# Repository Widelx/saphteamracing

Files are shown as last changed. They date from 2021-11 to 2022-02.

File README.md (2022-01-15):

# SaphTeamRacing
Course de voiture autonomes à laquelle participe l'IUT de cachan.
Année scolaire 2021/22.

Programmes MBED, Keil et Octave developpés par Guillaume de Maricourt.
Programmes d'interprétation développés par Antoine Beauvarlet.
PCB carte puissance et carte traitement développés par Axel Manadi.

Ces programmes et PCB sont réservés aux étudiants de l'IUT de Cachan uniquement.

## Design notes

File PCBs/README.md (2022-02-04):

# PCB - Carte DSICOF746NG

Ce dossier contient deux projets de PCBs
- Une première carte d'adaptation entre les différents modules et le microcontroleur F303K8.
- Une seconde carte (obsolète) d'adaptation entre les différents modules et la carte de contrôle DISCO F746-NG.

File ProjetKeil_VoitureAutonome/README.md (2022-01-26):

# Projet KEIL

Ce dossier contient une ébauche très succinte d'un projet keil qui initialise différents composants (PWM, UART).
Ce programme n'est absolument pas complet et n'est pas utile dans la version atuelle après migration sur la cible DISCO F746NG.
Cependant celui-ci à terme devrait être utile pour la carte KEIL développée.

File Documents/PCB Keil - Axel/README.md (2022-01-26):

Ceci contient le PCB ainsi que les shematics d'une carte Keil adaptée aux dimensions de la maquette de la voiture.

Logiciel : ALTIUM designer 2004

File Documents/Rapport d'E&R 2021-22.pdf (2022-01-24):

## Rapport d’Etude et Réalisation

## Année Universitaire 2021-2022, Semestre 3

# SAPH TEAM RACING

## Course de voitures autonomes

Présenté par : Antoine Beauvarlet,

## Axel Manadi, Guillaume Dumesnil

Janvier 2022

## Sous la direction de M. Martincic et M. Bellanger

Guillaume Dumesnil, Antoine Beauvarlet, Axel Manadi
Rapport E&R, S3
Janvier 2022 | 2

# Remerciements

Nous tenons à remercier toutes les personnes qui ont contribué au succès de notre projet et

qui nous ont aidés lors de la rédaction de ce rapport.

Nous voudrions dans un premier temps remercier M. Martincic, professeur d’Etude et

Réalisation à l’IUT de Cachan, pour sa patience, sa disponibilité et surtout ses judicieux

conseils, qui ont contribué à la réussite de ce projet.

Nous remercions notre professeur de Culture et Communication M. Bellanger qui nous a

guidé dans la rédaction du rapport.

Également, nous tenons à remercier M. Ardillier ainsi que tout le corps enseignant de l’IUT

de Cachan pour avoir assuré le bon déroulement de nos différentes séances et permis, à

terme, de mener à bien ce projet semestriel.

Enfin, merci à nos camarades de promotion avec lesquels nous avons échangé sur nos

projets respectifs.

# Résumé

Notre projet de troisième semestre consiste à créer une voiture électrique autonome

capable de se déplacer sans intervention humaine.

Pour ce projet, nous avions besoin de plusieurs cartes électroniques que nous avons

élaborées avec pour objectif de tenir dans le châssis du véhicule. Un moteur brushless

relié aux quatre roues motrices ainsi qu’un servomoteur assurent le déplacement de la

voiture. Tous les composants ont été assemblés sur un châssis de Lancia Delta de

modélisme.

Pour rendre le véhicule autonome, nous l’avons équipé de capteurs infrarouges et à

ultrasons ainsi que d’un LiDAR. Par ailleurs un module Bluetooth est connecté au

microcontrôleur afin d’assurer une transmission sans fil et de collecter les données perçues

en temps réel.

Pour la conception et la réalisation de ce projet, nous avons eu besoin de passer par

plusieurs logiciels : Altium pour la conception des cartes électroniques, Mbed Studio et

MBed.org pour la programmation des microcontrôleurs DISCO F746-NG ainsi que le logiciel

Octave pour la visualisation des données en temps réel.

# Sommaire

# Introduction

À l'IUT de Cachan dans le département GEII2 les étudiants de S3 réalisent un projet

semestriel qu'ils choisissent. Ce projet semestriel a pour objectif de mettre en application les

connaissances acquises en génie électrique (TEC*

1
, SA*, CE*), physique, mathématiques et

programmation (IENA*).

Notre groupe, constitué de trois élèves, s’est donné comme objectif de créer une voiture

autonome pour participer à une course organisée en avril 2022 où concourent diverses

écoles d’ingénieurs et universités. Dans ce contexte notre problématique est d’obtenir un

véhicule capable d’interagir avec son environnement sans opérateur humain, et sans

collision avec les autres véhicules ou obstacles.

Ce projet de voiture autonome nous a permis de travailler en petit groupe avec des sous-

tâches attribuées à chacun des membres. Cela permet d’appréhender concrètement

l’électronique, la programmation, la mécanique et surtout le travail en équipe.

Travailler en groupe permet de se répartir les tâches selon nos spécialités, afin de respecter

les délais et d’être plus efficace. De plus nous sommes obligés de rendre compte au groupe

et respecter nos engagements.

Bien entendu durant tout ce projet notre professeur peut être sollicité, afin de nous

accompagner et de nous faire progresser. Au début du semestre, chaque groupe d’étudiant

du semestre 3 a préparé une soutenance afin de présenter les objectifs de leur projet et ont

livré un diagramme de Gantt* prévisionnel.

Contrairement aux semestres précédents, ce projet nous plonge dans une situation presque

professionnelle : définir et répondre à un cahier des charges tout en prévoyant et respectant

les délais de livraison.

Dans un premier temps, nous présenterons la mécanique de la voiture, puis nous étudierons

les différentes cartes électroniques réalisées. Ensuite, nous examinerons comment la

réception des données constituant l’environnement est réalisée puis comment l’interprétation

de celles-ci s’effectue. Enfin nous conclurons.

1 Les mots accompagnés d’une * sont des mots définis dans le lexique à la fin de ce document.

# Présentation du projet

Lors du semestre 3 nous avons pu choisir notre projet : une course de voitures autonomes.

Ce projet, organisé depuis longtemps, consiste à récupérer le travail que le groupe de

l’année dernière a produit et le continuer. Ainsi notre groupe a pu, en s’appuyant sur le

rapport du groupe précédent, améliorer, repenser les concepts de programmation et

recommencer certaines parties.

Nous sommes partis d’un châssis de Lancia Delta de modélisme, imposé par le règlement

de la course, que nous avons adapté pour recevoir nos capteurs. Le travail du groupe

précédent ayant concerné l’assemblage du véhicule, cela nous a permis de nous focaliser

sur l’instrumentation de celui-ci.

Nous avons dû concevoir des cartes imprimées : carte de puissance et carte d’acquisition.

Puis mettre en œuvre des capteurs afin de modéliser l’environnement et générer une

réflexion sur les comportements de la voiture.

Ces 3 grandes tâches réparties sur le groupe ont été effectuées plus ou moins de façon

asynchrone. Les deux cartes imprimées sur lesquelles nous reviendrons plus tard, répondent

aux besoins suivants :

- Carte d’acquisition : contrôler les capteurs et modéliser l’environnement.
- Carte de puissance : générer une réponse au modèle et piloter les moteurs.

Toutes ces étapes sont détaillées dans la suite de ce rapport et en annexes²

## - Les règles de la course

## 1. Le cahier des charges

Lors de la course nous serons mis en compétition contre 5 autres véhicules autonomes. La

course s’effectue en 3 tours.

2 Afin de rendre synthétique ce document nous avons préféré placer certaines informations en annexe. De plus un repository GitHub a été mis en place pour transmettre la totalité de notre travail.

Pour y participer, nous devons nous plier au cahier des charges rédigé par les

organisateurs :

- Véhicule issu d’un kit de modélisme de Tamiya TT-02.
- Découpe de la carrosserie à condition qu’elle recouvre 80% du véhicule.
- Batterie de type NiMH* de 7,2V.
- Dimensions imposées afin d’être détectable (voir la figure suivante).
- Peinture n’absorbant pas les longueurs d’onde infrarouges.
- Contact bluetooth au moins 1 fois par seconde avec un appareil immobile (arrêt du

véhicule sinon).

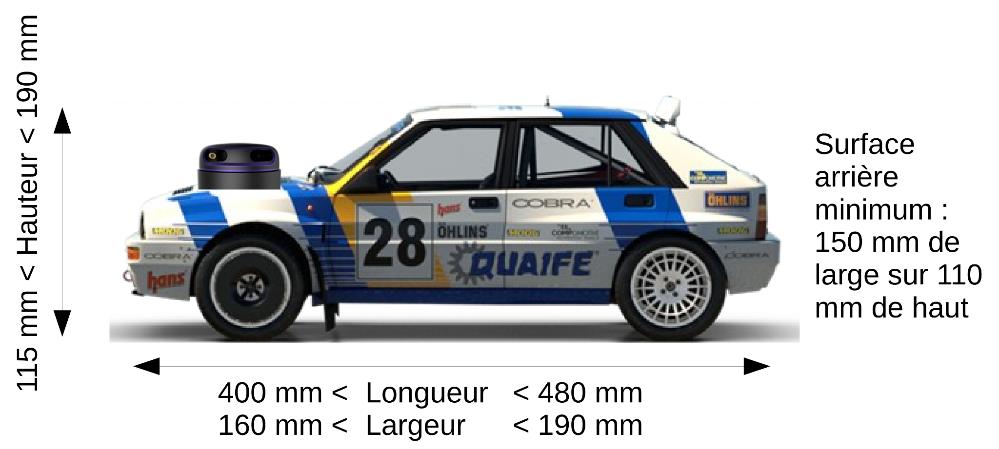
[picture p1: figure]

FIGURE 1: DIMENSIONS REGLEMENTAIRES DU VEHICULE

Concernant les capteurs, nous sommes libres dans le choix des capteurs tant qu’un capteur

LiDAR* est l'élément principal de détection de notre véhicule.

Pour s’assurer que les véhicule répondent au cahier des charges, les organisateurs

procéderont, lors de la course, à une homologation de ceux-ci.

## 2. Le circuit

Nous découvrirons le tracé du circuit le jour de la course. Actuellement nous sommes

uniquement informés des mesures de la piste. Celle-ci aura des bordures de 20 cm de

hauteur avec une largeur minimum en tout point de 50 cm. Par ailleurs elle contiendra des

obstacles conformément à l’exemple donné ci-dessous.

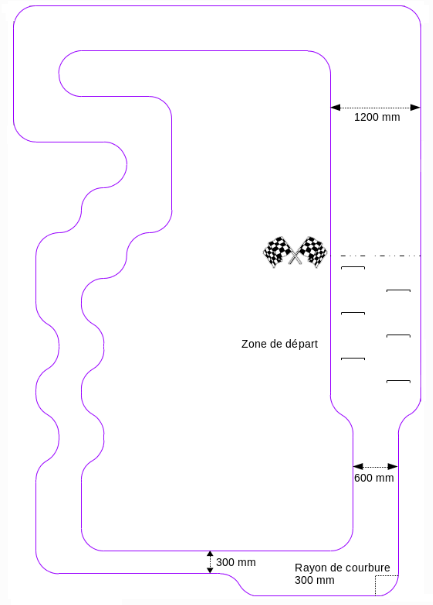
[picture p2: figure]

FIGURE 2: EXEMPLE DE PARCOURS FOURNI PAR LES ORGANISATEURS

Pour remporter cette compétition, il faut passer des qualifications sur une première piste,

chaque véhicule la parcourant seul. Deux passages sont exigés : un premier sans obstacle

puis un second avec. Chacune des qualifications nécessite deux passages successifs

réussis, c’est-à-dire sans collision avec les obstacles.

La somme des temps des deux passages détermine ensuite l’ordre de passage. Chaque

équipe dispose uniquement de 3 minutes pour préparer le véhicule sur la piste. Après ce

délai, aucune intervention humaine n’est tolérée.

## - Schéma synoptique du véhicule

Nous avons réalisé un schéma synoptique* afin de synthétiser et d’appréhender

l’assemblage des composants électriques qui constituent la voiture.

FIGURE 3: SCHEMA SYNOPTIQUE DU PROJET

FIGURE 4: LEGENDE DU SCHEMA SYNOPTIQUE

## - Diagramme de Gantt prévisionnel

Pour la soutenance de début de projet et répondre de manière professionnelle au cahier des

charges, nous avons réalisé un diagramme de Gantt prévisionnel. Celui-ci, bien qu’optimiste,

nous a permis de saisir une chose importante. En effet il faut prendre en compte qu’un projet

est souvent constitué de difficultés imprévisibles tant en quantité qu’en temps nécessaire

pour les résoudre. Le diagramme prévisionnel ci-dessous n’a effectivement pas pu être

respecté en totalité.

Cependant nous avons effectué plus de 80 % du prévisionnel, ce que l’on peut constater sur

le « diagramme de Gantt effectif » ci-dessous, qui reprend le calendrier que nous avons

effectivement suivi. Nous pouvons considérer notre estimation comme une réussite.

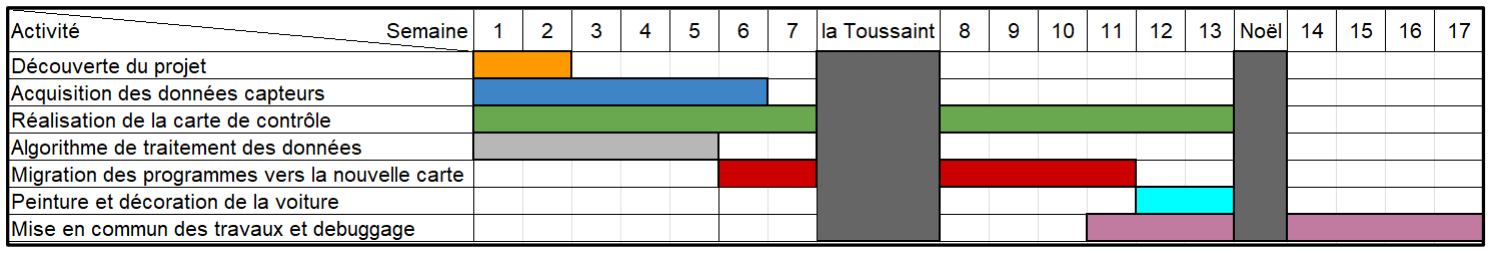
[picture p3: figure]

FIGURE 5: DIAGRAMME DE GANTT PREVISIONNEL

FIGURE 6: DIAGRAMME DE GANTT EFFECTIF

# Conception des PCB

## - Carte de puissance

Pour que le véhicule puisse se diriger durant la compétition, il faut créer une carte qui puisse

communiquer des instructions aux actionneurs présents sur le véhicule :

- Un servomoteur, pour la direction
- Un moteur brushless, pour avancer ou reculer.

La carte de puissance va communiquer avec les actionneurs grâce à un signal nommé PWM

(Pulse Width Modulation ou Modulation de Largeur d'Impulsion), qui est un signal alternatif

TOR (tout ou rien).

Ce signal alternatif, avec des vitesses de commutation très rapides, permet de d’approximer

la tension sur la liaison grâce notamment à l’inertie des moteurs : la tension ne devient plus

une série de commutations « 0/1 » mais une tension moyenne ajustable par un rapport

cyclique α.

FIGURE 7: EXEMPLE DE SIGNAL PWM.

Par ailleurs cette carte devra obéir aux instructions d’une unité de traitement comme une

autre carte par exemple. Il faut donc ajouter un moyen de communication.

## - Carte de communication

En plus de conduire le véhicule, nous avons besoin de traiter les données fournies par les

différents capteurs embarqués.

La carte communication recevra donc des informations de la part de :

- 1 capteur LiDAR (capteur principal).
- 3 capteurs à ultrasons (capteurs auxiliaires).
- 3 capteurs infrarouges (capteurs auxiliaires).

Dans cette carte nous allons téléverser un programme qui s’occupe de l'acquisition des

données, c'est-à-dire décoder ce que chaque capteur transmet. Celle-ci comprendra

également un algorithme décisionnel afin d’orienter le véhicule en fonction de

l'environnement : prendre un virage, éviter un obstacle ou une autre voiture par exemple.

On en déduit donc un rôle de carte maître vis-à-vis de la carte de puissance, car elle lui

donnera les instructions à exécuter. Enfin cette carte générera le signal PWM de commande

du lidar.

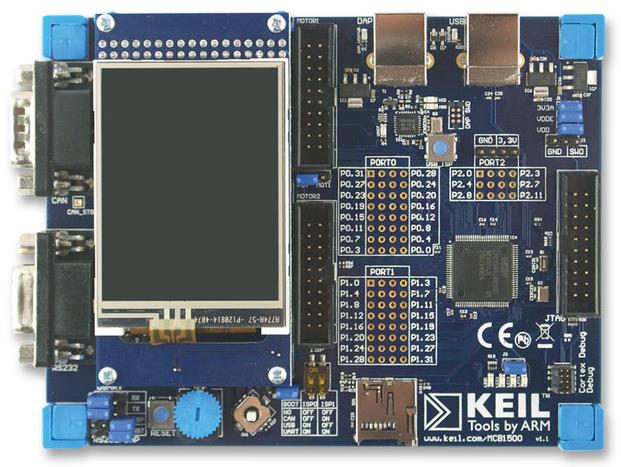
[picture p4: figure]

FIGURE 8: CARTE KEIL UTILISEE EN TP DE IENA

Nous avons commencé à réaliser cette carte, sur le modèle de la « carte Keil » de TP.

Malheureusement nous n’utiliserons pas cette dernière car elle ne sera achevée dans les

temps.

## - Conception des cartes

Pour concevoir ces deux cartes, nous avons utilisé le logiciel de CAO* : « Altium Designer ».

Plus précisément la version « 20.2.4 » du logiciel.

FIGURE 9: LOGO DU LOGICIEL ALTIUM DESIGNER

Une licence ainsi que des manuels d’utilisation nous ont été fournis, pour faciliter la prise en

main de cet outil professionnel.

Afin de trouver les composants nécessaires à la création de notre carte nous avons eu accès

aux bibliothèques de composants de l’université et des projets des années précédentes.

L’utilisation de ce logiciel est enrichissante : elle permet de découvrir le fonctionnement d’un

outil professionnel largement utilisé dans le monde de l’industrie.

Nous allons détailler, ci-dessous, les étapes à suivre pour réaliser un PCB.

## 1. Création d’un schéma

En premier lieu il faut créer un schéma : le but de cette opération est de placer les

composants et de les relier par des liaisons électriques théoriques. Cela permet de savoir

quels composants communiquent électriquement entre eux.

Notre professeur d’étude et réalisation, M. Martincic, nous a fourni le schéma des « cartes

Keil » utilisées à l'université durant les TPs d’IENA. Après une étude du schéma nous

remarquons que cette carte possède de nombreux composants superflus pour l’utilisation

que nous souhaiterions en faire.

Notre première mission consistait donc à supprimer les composants inutiles (et leurs

connexions) afin de simplifier le schéma et d’optimiser les performances de notre

microcontrôleur.

Une fois cette étape passée nous avons dû intégrer de nouveaux composants.

Un fichier contenant les fonctions de chaque broche de notre contrôleur nous a été fourni,

afin de relier chacun des composants à sa fonction associée.

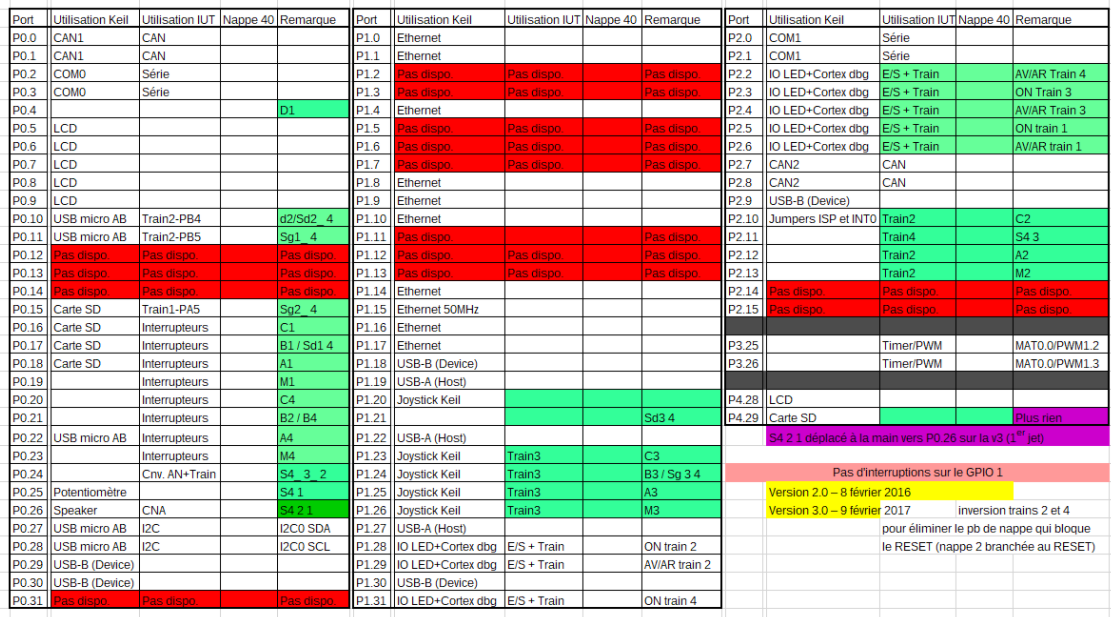
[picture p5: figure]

FIGURE 10: TABLEAU EXCEL DES FONCTIONS DU MICROCONTROLEUR

Nous avons laissé des ports CAN* pour que la carte puisse communiquer et recevoir des

informations ou instructions de la part d’un ordinateur (ou un autre microcontrôleur).

Après avoir relié chaque composant, nous pouvons passer à la deuxième étape : le câblage

du PCB*.

## 2. Câblage du PCB

Nous avons donc une nouvelle interface qui est une modélisation de la carte (réelle)

que nous allons imprimer. Pour que notre carte fonctionne correctement nous devons

effectuer le routage de celle-ci.

Cette étape, indispensable, consiste à tracer les pistes qui permettent de transmettre

l’information et d’alimenter les composants du circuit. Dans notre cas nous avons réussi à

nous limiter à une carte avec des pistes sur les deux couches externes (ce qui réduit

considérablement les coûts de production).

Positionner les composants sur les deux côtés de la carte permet une meilleure organisation

pour le routage. Le routage des cartes respecte une règle implicite et universelle : les pistes

ne doivent pas se croiser sur une même couche et ne doivent pas former d’angles droit.

Pour éviter que les pistes se rencontrent, on utilise des « via(s) » qui sont des outils qui

permettent de passer une connexion électrique d’une couche à l’autre.

Enfin quand le PCB est réalisé, nous devons faire un plan de masse. Cela consiste à

connecter chaque composant à une masse, pour que ceux-ci aient une tension de référence

commune et puissent fonctionner en régime nominal.

Remarque : Idéalement dans un véhicule il est recommandé de relier la masse au châssis

du véhicule. Dans notre cas le châssis est en plastique et cela ne fonctionnerait pas. Relier

la masse au châssis permet d’augmenter la surface de la tension de référence et d’être

moins sujet à des perturbations, par exemple les perturbations électromagnétiques que

génère le moteur.

Quand le plan de masse est finalisé, nous pouvons passer à la dernière étape : imprimer la

carte et souder les composants sur la carte.

## 3. Soudure des composants

Avant de procéder à la soudure, nous devons effectuer une commande qui va regrouper les

éléments de notre PCB. Cette commande demande d’inclure un fichier Gerber (format

standard, norme « d’impression ») qui pourra être reconnu et utilisé par les machines de

découpe des circuits.

Pour souder les composants nous utilisons la méthode de soudure à l’étain chaud : nous

fixons les différents composants du circuit à l’emplacement qui leur est dédié et nous venons

appliquer de l’étain sur les pattes des composants. Cela permet la connexion électrique

entre la piste et le composant.

Pour s’assurer du bon fonctionnement de la carte, nous effectuons des tests de connexion

des pistes. De plus nous devrons mettre en place des protocoles, simples, pour vérifier le

bon fonctionnement de chacun des composants assemblés.

FIGURE 11: IMAGE DE MICROSOUDURE

## - Problèmes rencontrés

Le problème principal des PCB est que les éléments constituants ces derniers fonctionnent

soit en 5, soit en 3,3 volts. Or notre alimentation fournit une tension de 7,2 volts, tension trop

importante qui pourrait abimer les composants.

Pour résoudre ce problème nous pensions tout d’abord ajouter un régulateur de tension qui

aurait eu pour rôle d’abaisser la tension d’alimentation. Cependant nous en avons discuté

avec notre professeur qui nous a déconseillé de le faire. Cela induirait des courants

importants qui provoquerait des perturbations sur les composants de notre carte.

Nous suivons donc le conseil de notre enseignant, et nous allons ajouter une carte

supplémentaire qu’il a réalisé pour pallier ce problème.

FIGURE 12: BATTERIE UTILISEE DANS NOTRE PROJET

Après avoir été capable de relier entre eux les composants nous devons les piloter. Ce

pilotage passe par la compréhension des composants que nous allons traiter. La partie

suivante traitera donc ce sujet.

# Modélisation de l’environnement

La voiture, pour interpréter et interagir avec son environnement, doit savoir comment celui-ci

est constitué. Pour ce faire le véhicule fait appel à divers capteurs qui permettent de

cartographier l’espace dans lequel il se déplace.

Cependant utiliser des capteurs implique divers délais qui compliquent la tâche :

- Un premier délai imposé par le principe de fonctionnement physique du capteur.
- Un second délai imposé par le type de transmission des informations.

Ainsi pour rendre efficace la tâche de reconnaissance de l’environnement, nous utiliserons 3

capteurs différents avec des positionnements sur le châssis bien spécifiques : 3 capteurs à

ultrasons et 3 capteurs infrarouges que nous appellerons des capteurs de proximité et un

LiDAR.

## - Le LiDAR

## 1. Principe de fonctionnement d’un LiDAR

Le capteur LiDAR pour « Light Detection And Ranging » est un système opto-électronique*

qui permet de mesurer des distances. Le fonctionnement repose sur un capteur infrarouge

monté sur un moteur : en actionnant le moteur, le capteur infrarouge tourne sur lui-même.

Le capteur infrarouge envoie ensuite des impulsions laser régulières qui sont perçues après

avoir été réfléchies sur un obstacle. Ainsi, plus la lumière émise met de temps à revenir, plus

l’obstacle est loin. Cela permet de faire des mesures de distance qui sont associées à un angle et de créer une carte de l’environnement très précise³

3 Le LiDAR utilisé dans notre cas est de la marque SLAMTEC, modèle A2, dont la documentation n’est pas simple à comprendre en début de projet. Nous essaierons d’être le plus précis possible pour simplifier la prise en main du projet.

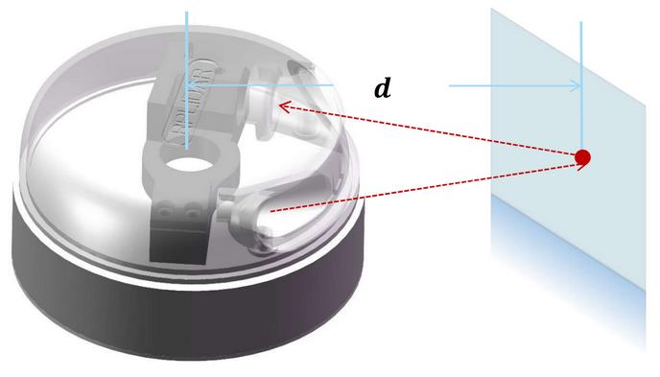
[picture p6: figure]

FIGURE 13: MODELE DE FONCTIONNEMENT DU LIDAR

FIGURE 14: REPRESENTATION PRECISE DU FONCTIONNEMENT DU LIDAR

Le LiDAR, en fonctionnement normal, effectue 2000 mesures par secondes. Le réglage du

signal PWM généré pour contrôler le moteur de celui-ci permet d’ajuster la précision du

LiDAR.

- Si le moteur tourne très vite nous aurons peu de mesures par tour mais beaucoup de

tours par seconde à analyser.

- S’il tourne très lentement nous aurons beaucoup de mesures pour un tour mais peu

de tours par seconde à analyser.

## 2. La transmission des informations

- L’interprétation des trames

La transmission des informations captées par le LiDAR se fait au moyen d’une liaison série

(RS232) dont nous étudierons le fonctionnement plus tard. La bonne compréhension des

données transmise nécessite de s’approprier le concept de trames (ou encodage

d’informations sur plusieurs octets) que nous allons détailler ici.

Une trame informatique est, par définition, « une structure de base d'un ensemble de

données encadrée par des bits de début et des bits de fin ». Cela veut simplement dire

qu’une trame est un assemblage de bits qui sont liés à diverses informations.

Dans notre cas, UNE trame transmise par le LiDAR contient 3 informations utiles associées à une mesure (ou un point⁴
).
- La qualité de la mesure.
- L’angle de la mesure.
- La distance associée à cet angle.

Cette trame est un assemblage de 5 octets avec la répartition de l’information détaillée sur la

figure suivante, selon la documentation du constructeur. De cette lecture on peut retenir la

chose suivante. Sur une trame constituée de 5 ∗ 8 = 40 bits nous avons :

- La qualité sur les bits 2 à 7 (6 bits).
- L’angle sur les bits 9 à 23 (15 bits).
- La distance sur les bits 24 à 39 (16 bits).

4 Par la suite nous supposerons qu’une mesure (une trame) correspond à un point (en coordonnées polaires).

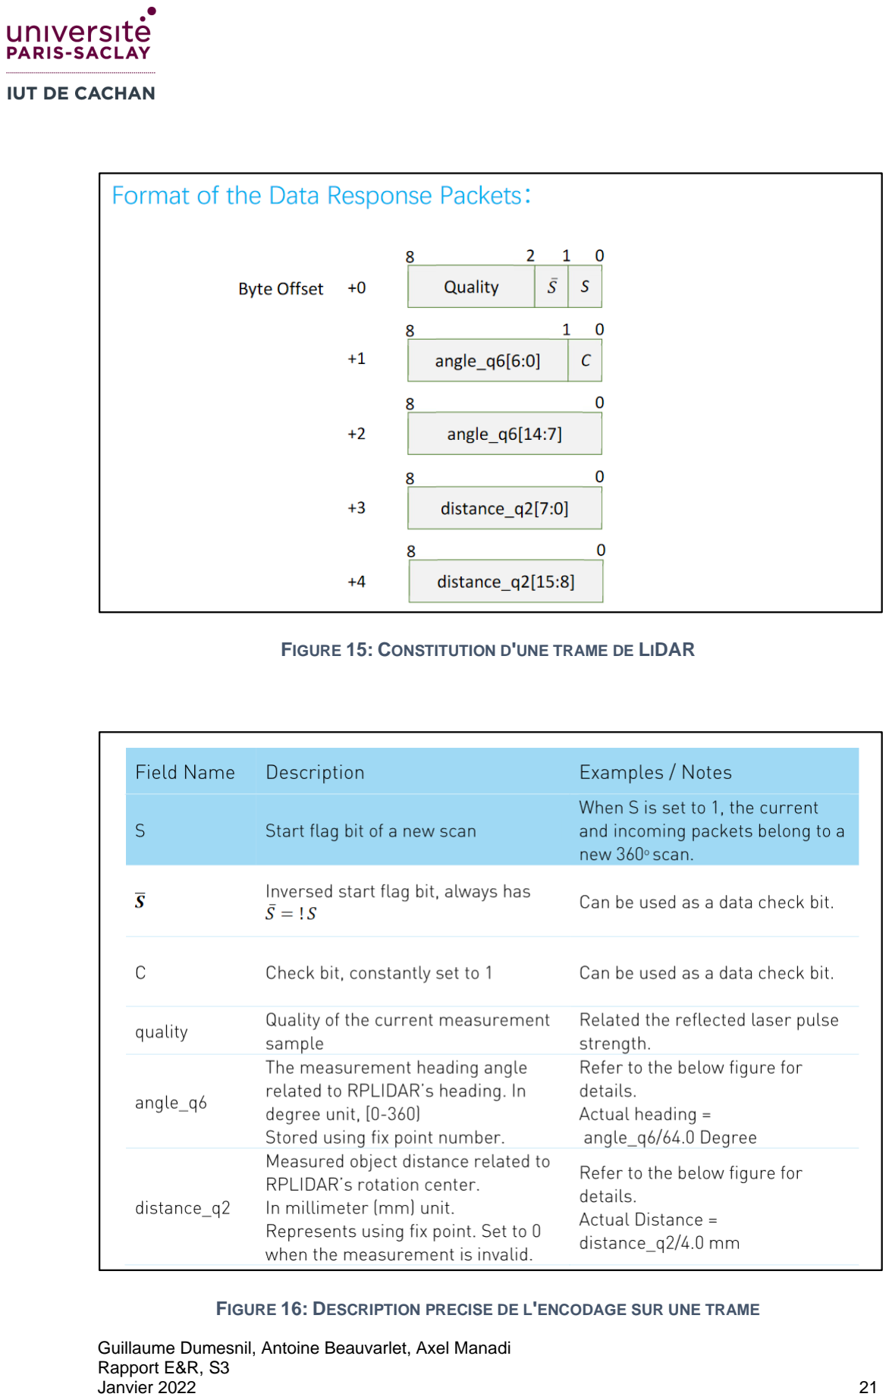
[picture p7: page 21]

FIGURE 15: CONSTITUTION D'UNE TRAME DE LIDAR

FIGURE 16: DESCRIPTION PRECISE DE L'ENCODAGE SUR UNE TRAME

Ainsi en réceptionnant les trames dans un tableau de 5 caractères (un caractère

correspondant à un octet) il est très simple de reconstituer la distance, l’angle et la mesure

d’un point. Voici trois exemples de fonctions qui reconstituent l’information en prenant les

octets correspondants en argument.

Remarque : Il existe cependant deux nuances essentielles pour décoder ces trames. La

valeur binaire de la distance doit être convertie en flottant puis divisée par 4. La valeur sera

alors en millimètres. De même pour l’angle avec une conversion en flottant divisée par 64 pour obtenir des degrés⁵

FIGURE 17: FONCTIONS DE DECODAGE DES TRAMES

On notera la présence d’une saturation numérique sur la valeur de la distance. Dans notre

cas voir à 16 m n’est pas utile et permettra une interprétation plus simple des données.

Nous verrons par la suite que selon le modèle d’exploitation des données, ces trames

contiennent deux autres informations utiles : S et /S ainsi que C. Cela permettra de mettre en place un algorithme de synchronisation ou de vérification de synchronisation⁶

5 Ces informations se trouvent sur la Figure 4.

### 6 Se référer à la sous-partie « Désynchronisation des trames »

Maintenant que nous avons compris de quoi est constituée une trame il nous reste à définir

les instructions à envoyer au LiDAR pour le piloter. Nous verrons la mise en œuvre de la

communication LiDAR<->Microcontrôleur dans la partie suivante.

- Les commandes pour piloter le LiDAR

Le LiDAR, pour fonctionner, doit recevoir des instructions de la part du microcontrôleur. Ces

instructions qui sont proches du concept de trames permettent de changer l’état du LiDAR.

Les instructions ont nous aurons besoin sont présentés ci-dessous avec leur instruction

machine associée.

FIGURE 18: TABLEAU DES INSTRUCTIONS MACHINE

On observe que l’octet n°1 est toujours le même : 0xA5. En effet cet octet quand il est

envoyé averti le LiDAR qu’il va recevoir une instruction dans la milliseconde suivante. Si

aucune information n’est envoyée (octet 2), le LiDAR reste dans son état actuel.

Sous cet aspect, piloter le LiDAR semble très simple. Malgré tout il existe des informations

importantes à savoir pour chacune des instructions.

- Utilité de la fonction Reset

La fonction Reset permet de redémarrer le système du LiDAR. Il peut être nécessaire

de le faire si l’on détecte un défaut de fonctionnement de la part du LiDAR. Par exemple si

l’on ne reçoit pas de réponse de celui-ci.

Conclusion : Faire un reset lors de la mise en route du LiDAR permet de s’affranchir de

certains problèmes.

- Différence entre les fonctions Scan et ForceScan

La fonction Scan nécessite que la vitesse de rotation du LiDAR soit stable avant que

celui-ci n’envoie des points en réponse à l’instruction. La fonction ForceScan permet de

s’affranchir de cette nécessité et permet d’avoir des mesures plus rapidement.

| Trame complète
Instruction | Octet 1 | Octet 2
Stop | 0xA5 | 0x25
Reset | 0xA5 | 0x40
Scan | 0xA5 | 0x20
ForceScan | 0xA5 | 0x21

Ainsi il semble préférable de toujours utiliser ForceScan et non Scan lors du déploiement du

logiciel pilote. Cependant la fonction ForceScan ne permet pas d’assurer la continuité des points⁷
, c’est-à-dire la stricte croissance de l’angle.

Conclusion : Il est préférable d’utiliser la fonction Scan lors du déploiement de la version

finale du software et ForceScan uniquement pour débugger.

Lorsqu’on lui envoie une demande de scan le LiDAR répond par une trame type. Celle-ci est

constituée de sept octets : deux octets de synchronisation et cinq octets (une trame

complète) pour indiquer l’instruction interprétée par le LiDAR.

Après cela le LiDAR envoie en continu des trames sans s’arrêter, sauf si on le lui demande.

Remarque : Il est important de comprendre qu’une trame équivaut à un paquet de 5 octets.

Ainsi un problème de synchronisation ou une perte de trame (non envoyée, mal

réceptionnée) entraine des interprétations erronées qui rendent l’utilisation du LiDAR impossible⁸

FIGURE 19: REPONSE DU LIDAR A UNE REQUETE "SCAN"

Maintenant que nous avons compris du point de vue théorique comment piloter le LiDAR et

interpréter ses données nous allons voir comment cela est réalisé en utilisant un

microcontrôleur.

## - Acquisition des données LiDAR

Afin de réaliser l’acquisition des points collectés par le LiDAR de façon efficace il est

nécessaire de définir plusieurs aspects de cette acquisition.

1) Le fonctionnement physique de la communication « microcontrôleur<->LiDAR ».
2) Les outils informatiques mis à disposition en C/C++.
3) Les couches de communication et les objectifs de notre programme.

7 Se référer à l’annexe « 1 : Continuité des points » pour plus d’informations à ce sujet.

### 8 Se référer à la sous-partie « Désynchronisation des trames »

De ces 3 points nous pouvons constituer des algorithmes, plus ou moins efficaces, qui

acquièrent les trames envoyées par le LiDAR. L’algorithmie de l’acquisition des points

constitue une partie en elle-même. Celle-ci reposant sur des bases nous allons voir, nous y

reviendrons donc plus tard.

## 1. Le protocole de communication : la liaison RS232

La liaison série RS232 asynchrone

9 est un type de protocole d’échange d’informations. Ce

protocole permet la communication entre deux modules avec un nombre de fils inférieur à

d’autres protocoles (I2C*, CAN).

Ce protocole permet une liaison bipolaire avec deux fils et unipolaire avec un fil, en plus de

la masse commune. La connexion entre les deux modules est relativement simple.

Contrairement aux protocoles I2C et CAN, la liaison série permet de relier uniquement deux

appareils entres eux.

La liaison série peut être vue comme un canal. En supposant un transmetteur TA et un

récepteur RB : on relie le canal d’émission de TA sur le canal de réception de RB. Ainsi B

peut écouter A au fur et à mesure que A envoie les informations. L’inverse est bien entendu

possible si B est capable de transmettre et A d’écouter. Cependant A et B doivent décider

d’une cadence commune de lecture et d’écriture.

La liaison série ne repose pas sur un fil qui constitue une horloge commune mais sur le fait

que l’émetteur et le récepteur se sont auparavant mis d’accord sur la cadence à suivre. On

peut comparer ce fonctionnement de cadence commune au morse : un opérateur doit savoir

différencier ce qu’est un trait d’un point. Si le récepteur (l’opérateur humain) ne sait pas

différencier les traits des points envoyés par l’émetteur (l’autre opérateur) cela pose un

problème.

On note usuellement TX et RX les pins des liaisons séries. De plus lorsque la liaison série

(du côté du récepteur) reçoit des bits celle-ci les stocke jusqu’à reconstituer un octet.

Remarque : La liaison avec le LiDAR est asynchrone. Cela sous-entend qu’il peut y avoir un décalage des bits au bout d’un certain temps d’utilisation de la liaison¹⁰

9 Nous appellerons par la suite cette liaison simplement « liaison série ». Celle-ci est peut aussi être appelée interface « UART ».

### 10 Se référer à la sous-partie « Désynchronisation de la liaison série »

FIGURE 20: CABLAGE D'UNE LIAISON SERIE

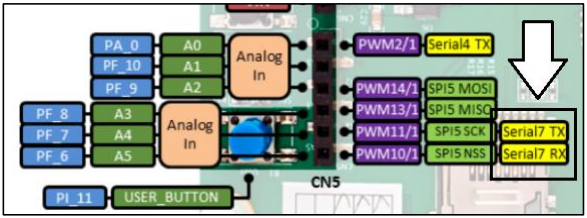
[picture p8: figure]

FIGURE 21: NOMS USUELS DONNES AU PINS QUI SUPPORTENT LA LIAISON SERIE

Ainsi après avoir établi une liaison physique entre le LiDAR et le microcontrôleur il est

nécessaire de pouvoir écrire dessus ou lire ce qu’on a reçu.

## 2. Les outils informatiques nécessaires au projet

Le microcontrôleur choisi pour toute la réalisation de ce projet (coté acquisition des données)

est un MBED DISCO-F746NG. L’idée à l’origine étant de migrer le code C++ en C pour un

processeur CORTEX M3 LPC1768 (cf. carte Keil). Cependant par manque de temps la

migration n’a pu être faite. Pour autant il est possible d’utiliser le microcontrôleur MBED NXP LPC1768 pour réaliser ces tâches sans migration de code¹¹
- Les interruptions et la liaison série

Lors du semestre 3, nous apprenons l’existence de fonctions d’interruptions. Sans rentrer

dans les détails ces fonctions sont, comme leur nom l’indique, des fonctions qui suspendent

temporairement la tâche qu’exécute le microcontrôleur. Cela permet au microcontrôleur

d’exécuter une autre tâche, plus importante, avant de reprendre là où il en était.

11 Documentation disponible sur le site : https://os.mbed.com/docs/mbed-os/v5.15/apis/index.html ➔ Attention : Version 5.15 de MBED OS.

Ainsi nous allons utiliser une fonction d’interruption dans ce programme : une interruption du

microcontrôleur déclenchée lorsqu’un caractère est arrivé sur la liaison série. Une fois cette

interruption déclenchée, on peut la traiter. « Traiter » entend ici « stocker le caractère » et

« s’acquitter de l’interruption »

12

FIGURE 22: CREATION DE LA LIAISON SERIE "SLIDAR"

FIGURE 23: CONFIGURATION DE LA LIAISON SERIE ET DE L’INTERRUPTION A EXECUTER

Ainsi on réalise trois tâches successives :

- Déclarer la liaison série avec les pins TXLIDAR et RXLIDAR : ces variables sont

définies dans un fichier d’entête (ou « header/.h »). On déclare en même temps que

l’horloge de fonctionnement mutuelle est de 115200 bauds*.

- Donner le format de la liaison série selon la documentation de MBED OS v5.15.
- Associer une fonction à l’interruption « caractère reçu » en passant comme

paramètre l’adresse de cette fonction (ici « getChar »).

Maintenant que l’on a créé la liaison série et donné un nom à la fonction d’interruption on

peut affirmer deux choses : le microcontrôleur est capable de communiquer avec le LiDAR

(liaison bipolaire) et celui-ci appellera systématiquement la fonction « void getChar(void) »

lors de cette interruption. Il faut maintenant stocker les caractères qui sont arrivés pour

pouvoir les traiter.

- Le buffer circulaire

Un « buffer » (ou tableau) est un espace mémoire alloué pour stocker des

informations. Ainsi un tableau de caractère pourrait être suffisant pour stocker les octets qui

arrivent sur la liaison série. Cependant si l’on en vient à saturer ce tableau il peut y avoir un

12 Cette notion sera précisée au cours du semestre 3 à l’IUT de Cachan, en cours de IENA.

phénomène de dépassement de capacité : on demande de stocker plus d’informations que

possible.

Cela présente un énorme problème : le microcontrôleur ne sait pas comment réagir et

prendra une décision qui nous est inconnue. Pour pallier ce souci on peut choisir d’utiliser

une autre structure de données : le « buffer circulaire ».

Le principe du buffer circulaire repose sur le principe que celui se rempli de façon cyclique.

Quand on arrive à la fin du tableau on recommence au début. Si celui-ci arrive à saturation

on peut choisir quoi exécuter :

- Ecrire l’informations reçu sur des informations non traitées (écraser des données

anciennes)

- Ignorer l’informations reçu tant que le buffer est saturé (rejeter des données récentes)

Le buffer circulaire respecte le principe de FIFO* qui permet de garder une continuité dans

l’arrivée des données.

FIGURE 24: SCHEMA FONCTIONNEL D'UN BUFFER CIRCULAIRE

Ainsi en liant ce type de structure à notre fonction d’interruption on peut stocker les octets qui

arrivent un à un en évitant tout comportement imprévisible. On profite aussi de l’aspect FIFO

qui évite de devoir manipuler un itérateur avec le risque de mal le manipuler. Il faut tout de

même noter que le buffer circulaire, plus complexe, introduit des délais plus importants qu’un

tableau simple.

FIGURE 25: DECLARATION D’UN BUFFER CIRCULAIRE (STOCKANT DES CARACTERES)

FIGURE 26: FONCTION D'INTERRUPTION QUI TRAITE LE CARACTERE DISPONIBLE SUR LA LIAISON

Après avoir réceptionné les octets, les avoir rassemblés et être capable de décoder les

trames il reste la question de savoir quoi en faire et comment les transmettre à la couche

d’interprétation.

## 3. Les couches de communications et les objectifs du programme

D’une part le microcontrôleur reçoit des octets un à un que le microcontrôleur doit décoder

(par paquet de 5 octets, c-à-d des trames ou des points). D’autre part, ces données doivent

être transmises pour être interprétées. Plusieurs possibilités ont été émises quant à l’envoi

des points collectés à la couche d’interprétation.

Il a été décidé plusieurs choses pour la conception de ces « paquets de points » :

- La nécessité d’un format simple qui soit abordable par n’importe quel type de

programmeur.

- Une quantité d’informations limitée pour faciliter et accélérer le processus de

traitement.

- Une conversion des angles dans un format adapté au traitement.
- Un protocole qui permette un transfert simplifié vers d’autres modules.

Pour répondre à ces critères nous avons décidé de stocker 181 points dans un tableau de

type flottants où l’indice du tableau correspond au degré scruté.

Effectivement seul l’avant de la voiture nous intéresse : il n’est donc pas nécessaire de

mémoriser ce qu’il se passe derrière le véhicule. De plus selon la figure suivante il convient

de changer le format de l’angle : le format fourni par le LiDAR ne correspondant pas à nos

besoins.

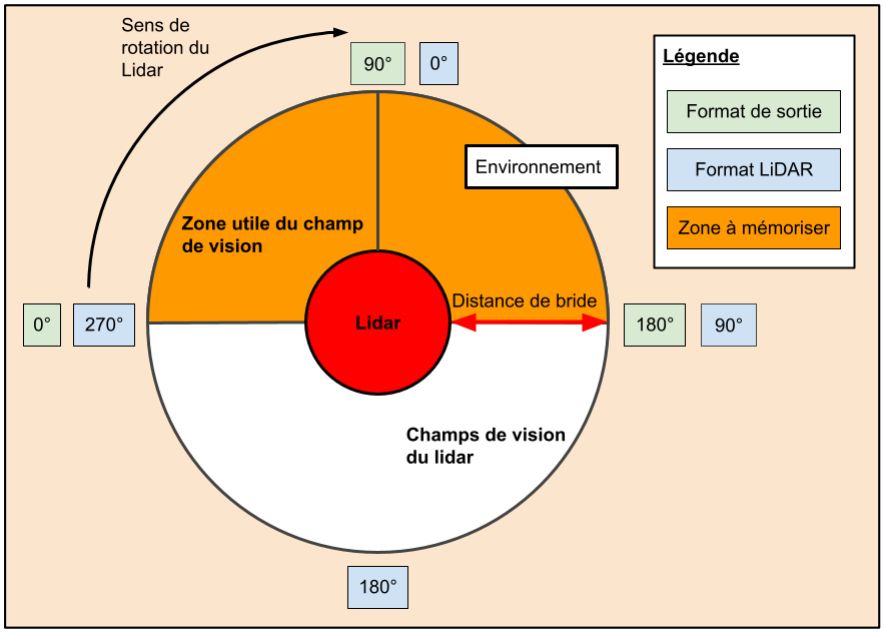
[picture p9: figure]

FIGURE 27: REPRESENTATION DE LA VISION DU LIDAR ET DES FORMATS D’E/S

On peut représenter le format de sortie des données sous une forme plus explicite.

FIGURE 28: REPRESENTATION EXPLICITE DU FORMAT DE SORTIE

Pour passer de la couche d’entrée à la couche de sortie il faut donc composer un algorithme

qui fasse l’interface entre les couches « d’entrée » et de « sortie ». Nous nommerons en plus des critères précédents d’autres critères afin de mesurer l’efficacité de notre algorithme¹³ :

- La rapidité d’exécution.
- Le temps de réponse du programme (temps mis pour reconstituer un tour complet).
- La fiabilité du programme face à des évènements aléatoires : perte de trames,

décalage des bits de la liaison asynchrone.

- La capacité mémoire occupée par le programme.

13 Se référer à l’annexe B2, « Synchronisation en temps réel » pour plus d’informations à ce sujet.

| Tableau de flottant de taille 181
Indice | 0 | 1 | … | 90 | 91 | … | 180
Flottant (distance) associée | Distance à 0° | Distance à 1° | … | Distance à 90° | Distance à 91° | … | Distance à 180°
Position par rapport à la voiture | Gauche | | | Devant | | | Droite

FIGURE 29: SCHEMA RESUMANT L'ACQUISITION DES DONNEES

## - Algorithmes de traitement des données

Après avoir établi les principes de fonctionnement de l’algorithme de traitement nous

pouvons nous atteler à le concevoir. Nous allons dans un premier temps étudier deux

modèles « primitifs » et un modèle plus complet.

Les deux premiers modèles bien que très simples en comparaison avec le dernier ont été

nécessaires. Ce sont eux qui ont servi de base d’apprentissage pour appréhender le LiDAR,

décrypter sa documentation complexe et permettre l’existence d’algorithmes* plus légers ou

rapides.

Cette partie, moins rédigée et plus schématisée tentera d’aborder un problème paradoxal

soulevé par le LiDAR. Ce capteur envoie une quantité d’information très importante

(2 000 points par seconde). Cependant la gestion plus ou moins bonne de ces données vient

ralentir l’acquisition des points et donc la prise de décision.

## 1. Acquisition à durée fixe

Le premier modèle consiste à se déconnecter puis se reconnecter de façon régulière pour

obtenir les points qui constituent l’environnement. Ainsi on alterne entre les commandes

« start » et « stop » pour obtenir une quantité finie de points Np sur une durée θT. Après

avoir acquis ces points, on les traite tous : on isole ceux qui nous intéressent, si possible les

plus récents. Puis on recommence indéfiniment.

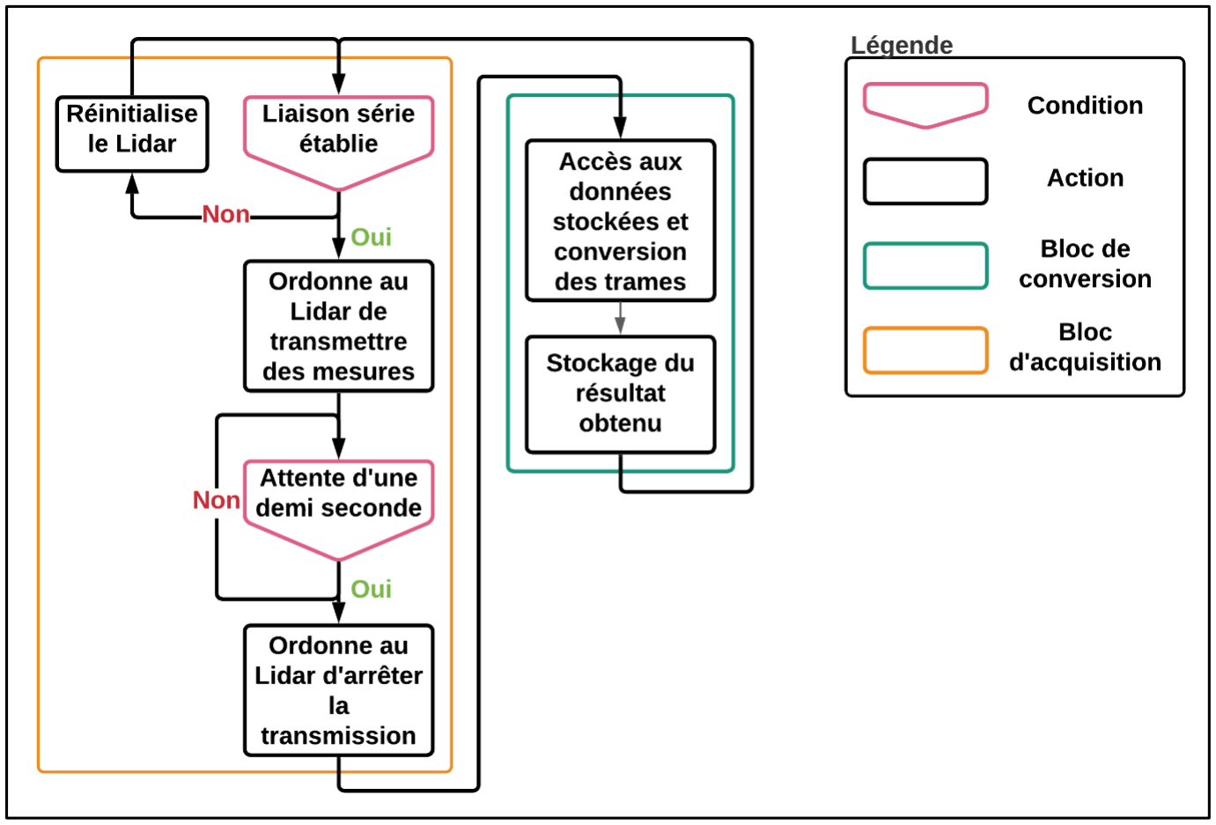
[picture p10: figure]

FIGURE 30: ALGORIGRAMME DU MODELE N°1

Avantages

- Simple à mettre en œuvre.
- Permet de comprendre comment fonctionne le LiDAR et confirmer son mode de

fonctionnement.

Défauts

- Lent à l’exécution.
- Enregistre plusieurs tours à la chaine quand seulement le plus récent nous intéresse.
- Le temps arbitraire d’une demi-seconde n’est pas suffisant. En réalité on constate

que : Tacquisiton > 0,8s

## 2. Acquisition avec boucle de contrôle « temps réel »

Le second modèle, un peu plus complexe en comparaison au premier, repose sur le même

principe d’acquisition avec l’alternance entre les commandes « start » et « stop ». La

différence étant que la durée d‘acquisition θT n’est plus fixe mais variable. Ainsi on décode

en « temps réel » les points qui arrivent. Cela est possible car Tacquisition trame ≫

Tconversion trame. Ainsi on peut récupérer les points, les décoder et les stocker au fur et à

mesure qu’ils arrivent. On obtient donc un modèle plus efficace que le premier.

Cependant le principe de connexion/déconnection n’est pas très efficace : en effet ordonner

au LiDAR de se mettre en mode « acquisition » a un coût en temps (valeurs mesurées

expérimentalement) :

- De l’ordre de 0,3s pour l’instruction ForceScan.
- De l’ordre de 0,7s pour l’instruction Scan.

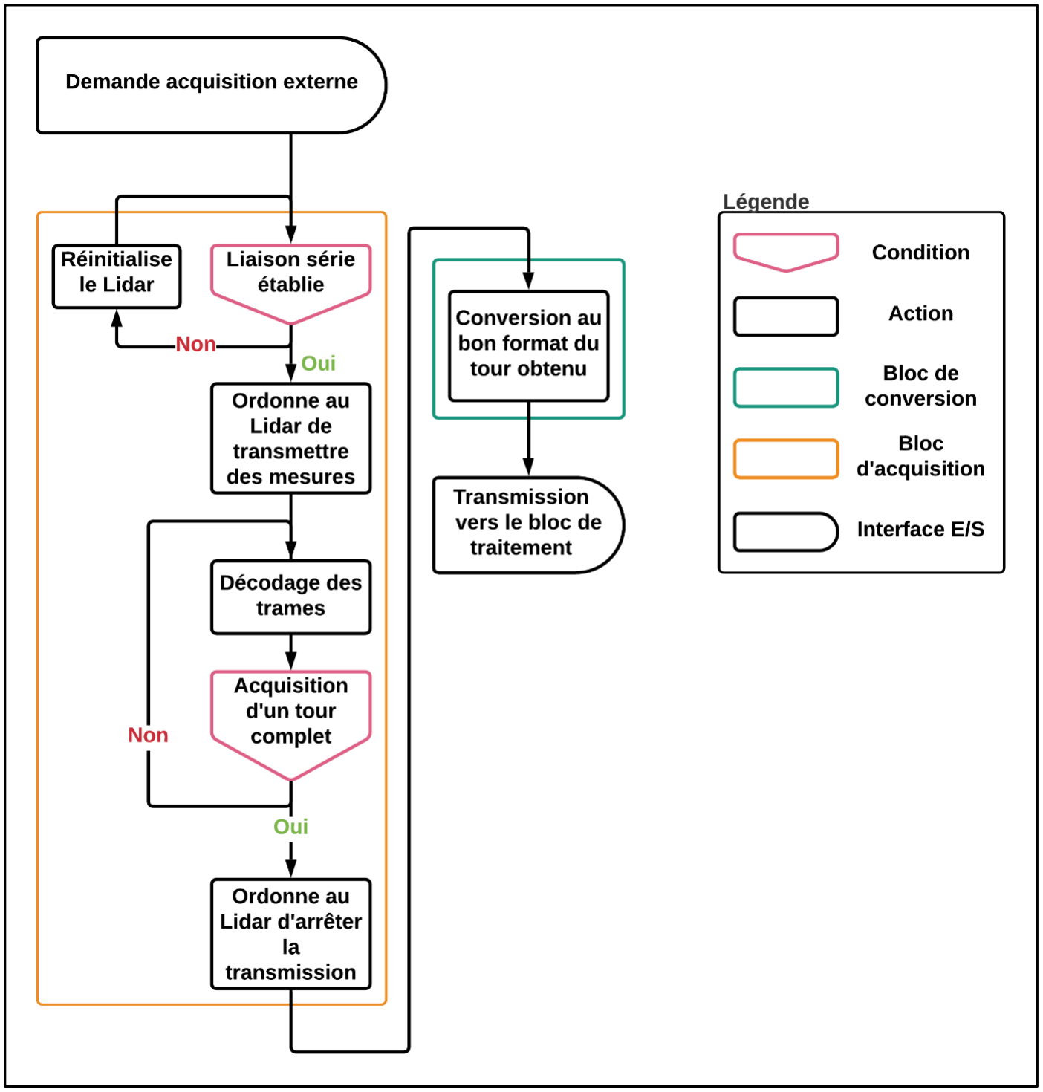
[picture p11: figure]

FIGURE 31: ALGORIGRAMME DU MODELE N°2

Avantages

- Plus rapide que le précédent.
- N’enregistre qu’un seul tour et un tour « complet ».
- Transmet toujours le tour le plus récent.

Défauts

- Bien que plus rapide que le modèle précédent celui-ci reste lent à l’exécution.
- Compliqué à mettre en œuvre.

## 3. Acquisition avec rejet de trames et boucle de contrôle « temps

## réel »

Ce modèle qui diffère très peu du précédent permet d’éviter les temps longs d’attente

générés par le modèle de connexion / déconnexion. Celui-ci consiste à rejeter les trames

une à une tant qu’il n’y a pas de demande d’acquisition de tour : cela est géré par la fonction

d’interruption. Cependant si une demande d’acquisition est adressée les trames sont traitées

et le dernier tour disponible est renvoyé.

FIGURE 32: ALGORIGRAMME DU MODELE N°3

Avantages

- Beaucoup plus rapide que les algorithmes précédents.
- N’enregistre qu’un seul tour et un tour complet.

- Transmet toujours le tour le plus récent.
- Variante de l’algorithme numéro 2.

Défauts

- Risque de désynchronisation très élevé.
- Peu robuste. En cas de désynchronisation, aucun contrôle ne permet d’en être

informé.

- Nécessité de reconnexion avec le LiDAR toutes les 10 secondes pour palier au

décalage des bits de la liaison série asynchrone.

Nous avons donc proposé des modèles d’algorithmes de plus en plus efficace. L’acquisition

d’une quantité importante de données n’étant pas simple, l’optimisation est primordiale.

Cependant certains problèmes persistent et ces algorithmes pourraient être encore

améliorés.

D’autres outils informatiques pourraient être utilisés comme le multitâche, la DMA. Par

ailleurs un autre protocole (plus complexe) de transmission existe : le LiDAR met à

disposition un mode « express scan » qui permet de passer de 2000 à 4000 points par

secondes. Par manque de connaissances nous ne détaillerons aucune de ces notions

citées.

## - Les difficultés rencontrées

## 1. Cout en temps de la méthode « start/stop »

Dans la partie précédente nous avons abordé le problème de la méthode « connexion

déconnection » qui vient rajouter un temps considérable du au changement d’état du LiDAR.

Ce temps peut être mis en évidence à l’aide de « timer » qui mesurent le temps de réception

des trames. On constate que le premier point est réceptionné après un délai important

d’environ 0,25 secondes.

Cependant la réponse du LiDAR à la requête est immédiate : « 0xA5 0x5A » pour établir la

transmission. Puis « 0x05 0x00 0x00 0x40 0x81 » pour confirmer que la requête reçue est la

bonne. Il y a donc un délai entre la réception de la requête et la mise en œuvre de celle-ci.

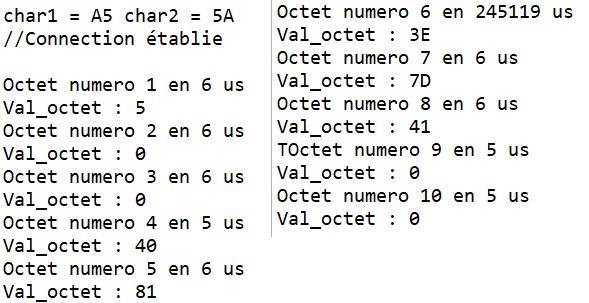
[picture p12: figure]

FIGURE 33: TEMPS D'ACQUISITION DES 10 PREMIERS OCTETS (INSTRUCTION FORCESCAN)

En ForceScan on constate que le temps est de 245119μs ≈ 0,25s. Pour une requête de

Scan ce temps est plus long (environ 0,6s).

## 2. Désynchronisation de la liaison série

Passé un certain délai, d’environ 15 secondes, la liaison série se désynchronise. De ce fait

on récupère des points convertis qui sont aberrants : par exemple de angles de 520 degrés.

Remarque : Avec notre professeur nous avons soulevé l’hypothèse suivante, cependant

nous n’avons aucune certitude de ce qu’il se passe réellement. Les drivers de la liaison série

devraient d’eux-mêmes gérer ce type de problème. Une étude plus poussée serait

nécessaire.

Cet effet est dû au type de liaison. Dans une liaison série il n’y a pas d’horloge commune

mais deux horloges respectivement égales (ou pas) : l’une chez l’envoyeur et l’autre chez

l’émetteur. Cependant ces horloges ne sont pas exactement les même car leur calcul repose

sur la fréquence de fonctionnement des quartz qui constituent l’horloge de référence des microcontrôleurs¹⁴

14 Cette notion sera précisée au cours du semestre 3 à l’IUT de Cachan, en cours de IENA.

La formule permettant de calculer le nombre de bauds est la suivante.

Baudrate =

Pclk

16 ∗ (256 ∗ DLM + DLL) ∗ (1 +

DIVadd val
MULval

)

Avec :

- Pclk l’horloge du microcontrôleur en Hz
- Baudrate en bits/secondes.

On peut sans calcul en déduire que plusieurs valeurs des paramètres permettent d’atteindre

115 200 bauds, de façon plus ou moins précise. Ainsi une tolérance existe entre

Baudthéorique et Baudeffectif. Cette tolérance est de l’ordre d’un pourcent au maximum. C’est

ce décalage entre les deux horloges qui au bout d’un certain temps entraine un décalage

des bits. Les octets entre l’émission et la réception sont alors différents et la liaison n’est plus

exploitable.

Pour pallier ce problème nous relançons la connexion entre le LiDAR et le microcontrôleur

régulièrement, environ toutes les 10 secondes.

## 3. Désynchronisation des trames

Les algorithmes présentés ne sont pas suffisamment robustes à l’état actuel : ils ne

permettent pas de vérifier qu’un octet constituant une trame n’a pas été perdu entre

l’émetteur et le récepteur. Cela aurait pour effet de décaler les octets qui constituent les

trames : on croit avoir l’octet 0 de la trame mais celui-ci a été « perdu ». En réalité on a

l’octet 1 qu’on croit être le 0 et ainsi de suite : la conversion des trames en point devient

faussée.

Des repères de vérifications des octets qui constituent les trames sont malgré tout

disponibles et un algorithme de vérification de la synchronisation serait souhaitable. Celui-ci

pourrait s’appuyer sur les 3 informations suivante :

- Le bit C toujours égal à 1.
- Les bits S et /S avec la règle qui s’applique selon la documentation.
- La valeur entière de l’angle avec : 0 ≤ Angle < 360.

Hypothétiquement on pourrait aussi vérifier l’équation de récurrence suivante :

Angleprécédent < Angleactuel pour S = 0 et S̅= 1

Cependant il été constaté qu’il y a parfois des sauts de valeur en ForceScan : la stricte

croissance de l’angle n’est pas vraie. On suppose qu’en Scan cela ne devrait pas arriver

mais aucune vérification n’a été faite.

FIGURE 34: DESCRIPTION COMPLETE D'UNE TRAME POUR OPTIMISATION

## 4. Optimisation des conversions

Dans un souci d’optimisation avec, à terme, un microcontrôleur sans FPU* il est préférable

de transformer les opérations de division par des décalages de bits (shifts).

En effet le degré de précision de la distance a été considéré comme suffisant en millimètre.

De même selon le protocole de transmission des données seul la partie entière de l’angle

nous intéresse. On rappelle qu’en programmation diviser par une puissance de 2 revient à

faire un décalage binaire vers la droite de cette même puissance.

Ainsi on omet la précision décimale d’une valeur pour gagner en nombre d’instructions

élémentaires. Le gain est considérable et ne devrait pas être négligé !

Octet | Octet 4 | Octet 3
Bit n° | 39 | 38 | 37 | 36 | 35 | 34 | 33 | 32 | 31 | 30 | 29 | 28 | 27 | 26 | 25 | 24
Info associée | D D D D D D D D D D D D D D D D

Trame complète constituée de 5 octets

Partie entière de la distance

Octet | Octet 2 | Octet 1
Bit n° | 23 | 22 | 21 | 20 | 19 | 18 | 17 | 16 | 15 | 14 | 13 | 12 | 11 | 10 | 9 | 8
Info associée | A A A A A A A A A A A A A A A | | | | | | | | | | | | | | | C
| Poids fort Poids faible
| Partie entière de l'angle
Poids fort | Poid faible
| Octet | | Octet 0
Bit n° | 7 | 6 | 5 | 4 | 3 | 2 | 1 | 0
Info associée | Q Q Q Q Q Q | | | | | | /S | S
| P. fort P. faible

# Les capteurs PING et infrarouges

## - Présentation des deux capteurs

Les capteurs complémentaires utilisés pour compléter l’acquisition de l’environnement sont

des capteurs à ultrasons et des capteurs infrarouges. Ceux-ci permettent d’épauler le LiDAR,

de confirmer son acquisition ou de la contredire selon le cas de figure. Ces capteurs dits de

« proximités » présentent l’avantage d’être très fiables et d’avoir des temps d’acquisition de

l’environnement constants.

On peut supposer un guidage « primitif » (sous-entendu court terme) issu des données de

ces capteurs de proximité et un guidage « poussé » (sous-entendu long terme) qui s’appuie

sur les données du LiDAR.

L’étude de ces capteurs sera moins complète en comparaison avec celle du LiDAR : ces

capteurs sont bien moins complexes.

## 1. Le capteur PING

Le capteur à ultrason est un capteur qui permet de connaitre la distance entre lui et un objet

qui se trouve dans son champ de vision (ou de rayonnement). Le capteur envoi un ultrason

qui est réfléchi sur l’objet : le temps entre l’émission et la réception permet de mesurer la

distance avec l’objet. Plus la distance avec l’obstacle augmente, plus la largeur de

l’impulsion reçue augmente : ainsi un obstacle proche sera détecté plus rapidement qu’un

obstacle éloigné.

Remarque : La propagation du son est très lente en comparaison avec la lumière. Ainsi les

capteurs à ultrasons que nous utilisons permettent de faire, au maximum, 20 mesures par

secondes.

Les capteurs à ultrason utilisés permettent en revanche d’avoir un secteur angulaire assez

large et d’avoir une idée globale de l’environnement en une mesure. Ceux-ci seraient très

utiles pour savoir si une mesure d’urgence est à prendre : s’arrêter, braquer les roues,

décélérer fortement.

FIGURE 35: COMMANDE ET REPONSES D'UN CAPTEUR A ULTRASONS

On observe que la commande des ultrasons se fait en deux temps : envoyer une impulsion

de start de 10 µs puis recevoir une impulsion. Cela demande d’utiliser au moins 2 pins GPIO

pour chacun des ultrasons.

Cependant on pourrait limiter le nombre de PINs de commande. En reliant la commande des

ultrasons à une ligne commune, on peut envoyer une impulsion de 10 µs qui sera perçue par

plusieurs capteurs ultrason.

## 2. Le capteur infrarouge

Les capteurs infrarouges sont extrêmement rapides et fournissent une mesure analogique

qui correspond à la distance entre le capteur et l’obstacle le plus proche. Ceux-ci permettent

un guidage très simple et très rapide. D’une part ils permettent de prendre des mesures

d’urgences, d’autre part de guider le véhicule quand aucune autre information n’est

disponible.

Le principal désavantage de ces capteurs repose sur le secteur angulaire qu’ils couvrent :

ceux-ci ne voient que devant eux.

## - Utilité des capteurs de proximité

Ces capteurs peuvent sembler dérisoires après toute l’étude sur le LiDAR. Cependant deux

problèmes viennent être résolus par ces capteurs : la durée longue d’acquisition du LiDAR et

les problèmes de soulèvement du châssis.

Comme vu précédemment, les données LiDAR selon l’algorithme utilisé, peuvent mettre plus

ou moins de temps à arriver à la partie décisionnelle. Ces capteurs de proximité sont très

rapides en comparaison et permettent de réagir vite.

De plus, si la voiture subit un choc ou accélère d’un coup, le châssis peut se soulever et

mener à un LiDAR qui pointe vers le ciel ou le sol : celui n’est alors pas du tout exploitable.

En venant épauler le LIDAR, ils peuvent confirmer ou contredire ce que le LiDAR croit voir.

Si plusieurs processus différents arrivent à la même conclusion alors l’information transmise

est fiable. Sinon il est préférable de croire les capteurs de proximité plus fiables et robustes à

la casse.

## - Positionnement des capteurs

Nous avons dû faire des choix afin de positionner les capteurs de proximité. Le but étant de

limiter leur nombre en se concentrant sur les secteurs angulaires ou l’information est la plus

utile.

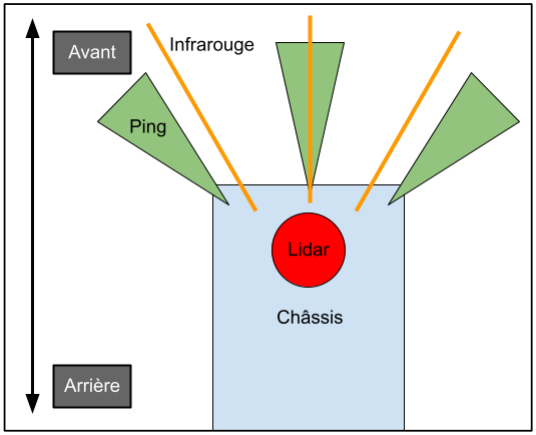
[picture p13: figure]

FIGURE 36: PLACEMENT DES CAPTEURS SUR LE CHASSIS

Remarques :

- Dans cette partie nous ne traitons aucunement les algorithmes de récupération des

informations des capteurs de proximité. Cependant il existe un répertoire GitHub qui

comprend plusieurs fonctions à ce sujet, qui sont détaillées dans les fichiers README

correspondant (voir annexe A1).

- Nous n’avons pas abordé le contrôle des moteurs. Cependant des fonctions ont été

réalisées et testées et sont disponible sur ce répertoire. L’annexe C explique comment

celles-ci ont été réalisées.

- Nous ne parlons pas non plus de possibles capteurs arrière pour nous sortir de situations

où il n’y a aucun autre choix que reculer. Cela reste à déterminer : quel capteur, quelle

quantité.

- Nous n’abordons pas un processus complémentaire à l’acquisition des données LiDAR.

Celui de la complétion des points : si certains angles n’ont pas reçu de distance associée

alors cet angle aura comme valeur celle de l’angle précédent.

# Le pilotage

## - Le traitement des données du LiDAR et des ultrasons

## 1. Les données du Lidar

Comme vu précédemment, le LiDAR récupère uniquement un secteur angulaire de 180

degrés (figure suivante) : cela correspond à l’avant de la voiture. Pour le format de

transmission, les points acquis par le LiDAR sont stockés dans un tableau de 181 cases.

L’index du tableau correspond à l’angle de la mesure et, la valeur stockée (pour cet indice)

correspond à la distance mesurée.

FIGURE 37: REPRESENTATION DE LA PLAGE DE MESURE DU LIDAR

Angle α; Distance; associée

FIGURE 38: TABLEAU REPRESENTANT LA DISTANCE EN FONCTION DE L’ANGLE DU LIDAR

## 2. Les données des capteurs à ultrasons

Les capteurs à ultrasons couvrent une plage de mesure restreinte ce qui impose de les

positionner de manière efficace tout en limitant leur nombre. On optimise ainsi la zone utile

de ces capteurs de proximité.

Les capteurs à ultrasons agissent comme des détecteurs de présence et renvoient la

distance associée à l’obstacle le plus proche. Par conséquent, cette distance renvoyée par

les capteurs couvre un secteur angulaire plus large que le LiDAR : cette valeur doit donc être

imposée à chaque angle de la plage de mesure.

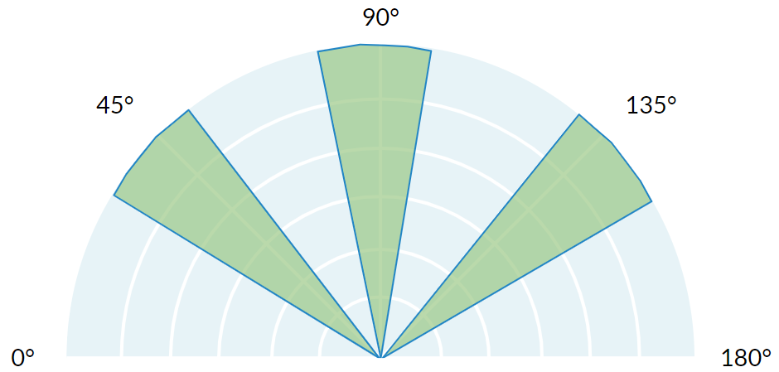
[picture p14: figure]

FIGURE 39: PLACEMENT DES CAPTEURS A ULTRASONS EN FONCTION DES PLAGES DE MESURE

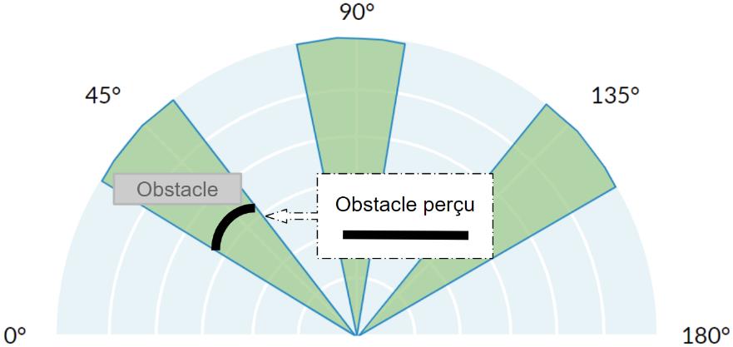
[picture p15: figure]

FIGURE 40: COMPORTEMENT D’UN CAPTEUR A ULTRASONS FACE A UN OBSTACLE

Les capteurs à ultrasons couvrent une plage de valeurs (un secteur angulaire). Pour être

consistant il est préférable de garder le même format de stockage que celui du LiDAR. La

distance mesurée sera donc appliquée à la plage de valeurs du tableau.

Angle α | 0° ~ 29° | Plage 1 | 61°~ 75° | Plage 2 | 105°~ 120° | Plage 3 | 150°~ 180°
Distance associée | | Distan ce 1 | | Distan ce 2 | | Distan ce 3

FIGURE 41: TABLEAU REPRESENTANT LE STOCKAGE DES MESURES DES ULTRASONS

## 3. L’association des capteurs

Sur notre véhicule, plusieurs capteurs viennent remplir la même tâche : détecter les

obstacles. Il y a donc des conflits de mesures lors de l’association des valeurs du LiDAR et

des ultrasons. Il est nécessaire de mettre en place un moyen de trier ces informations en

répondant aux questions suivantes :

- Quelle est la tolérance si les deux valeurs fournies divergent peu.
- Faut-il réagir de manière spécifique quand les valeurs divergent beaucoup, par

exemple : s’arrêter.

- Quel processus est le plus susceptible d’avoir raison.

De nos choix et réponses à ces questions, les mesures des capteurs à ultrasons viennent

recouvrir les mesures du LIDAR quand l’écart de valeurs est trop important.

En effet le LIDAR sera forcément soumis à des oscillations dues aux accélérations positives

et négatives.

Distance LiDAR | Distance ultrasons

FIGURE 42: EXEMPLE DE SUPERPOSITION DES MESURES

## - Le lissage des données reçues

Lors de son acquisition, le LIDAR peut parfois renvoyer des valeurs non cohérentes : c’est à

dire que sur un ensemble de point de même ordre de distance, un point est renvoyé à l’écart.

Pour corriger ce problème et pour tous les points de mesure, on programme un vérificateur

qui récupère les points PN, PN+1 et PN+2.

Si le rapport PN+1
PN

est dans une gamme de ± 5% et que le point PN+1 est dissident alors on

vient récupérer la distance du point PN et celle du point PN+2. On prend alors la moyenne de

ces deux points et on l’assigne à la valeur de la distance du point PN+1. Ainsi le point PN+1

est « équidistant » aux points PN et PN+2.

## - L’angle des roues, fonction du traitement des ensembles

## 1. Changement du format des coordonnées

Pour pouvoir être manipulées, il est nécessaire de récupérer la position cartésienne des

points : les données des points fournies par le LiDAR sont en coordonnées polaires. En utilisant les formules de trigonométrie on peut récupérer les coordonnées du point P(x ; y) en

coordonnées cartésiennes.

Angle α

0° ~

29°

Plage

1

61°~

75°

Plage

2

105°~

120°

Plage

3

150°~

180°

ypoint = distance ∗ sin(α)

xpoint = distance ∗ cos (α)

FIGURE 43: REPRESENTATION DE L'ORDONNEE D'UN POINT

Avec leurs coordonnées cartésiennes, il est possible de connaître l'écart entre deux points et également l’écart relatif : c'est à dire la valeur du rapport PN+1
PN

Ce rapport permet de

connaître le pourcentage d’écart entre deux points. Ainsi on établit un pourcentage de

tolérance qui définit si le point PN+1 est suffisamment proche du point PN. Si c’est le cas les

deux points font partie d’un ensemble commun, sinon ils font partie de deux ensembles

distincts.

Nous allons illustrer ce concept avec un exemple dont on donne les paramètres suivants :

P(%)tolérance = ± 5%, Y(PN) = 100 cm, Y(PN+1) = 103 cm

Le rapport PN+1
PN

est égale à 103 %.

Soit Y(Pn+1

) = Y(PN) + 3%

3% étant inférieur à 5% on considère que ces deux points font partie d’un même ensemble

(un mur de la piste par exemple).

## 2. La notion d’ensemble vide

Nous n’exploitons pas toutes les valeurs que peut fournir le LiDAR, nous y appliquons une

saturation numérique. Pour toutes valeurs de distance au-dessus de la saturation, on vient

remplacer la distance par -1. Ce changement permet de définir des zones de « vide » c’est-

à-dire des espaces sans obstacles proches.

Il est donc possible de différencier les ensembles « vides » des ensembles « obstacles ».

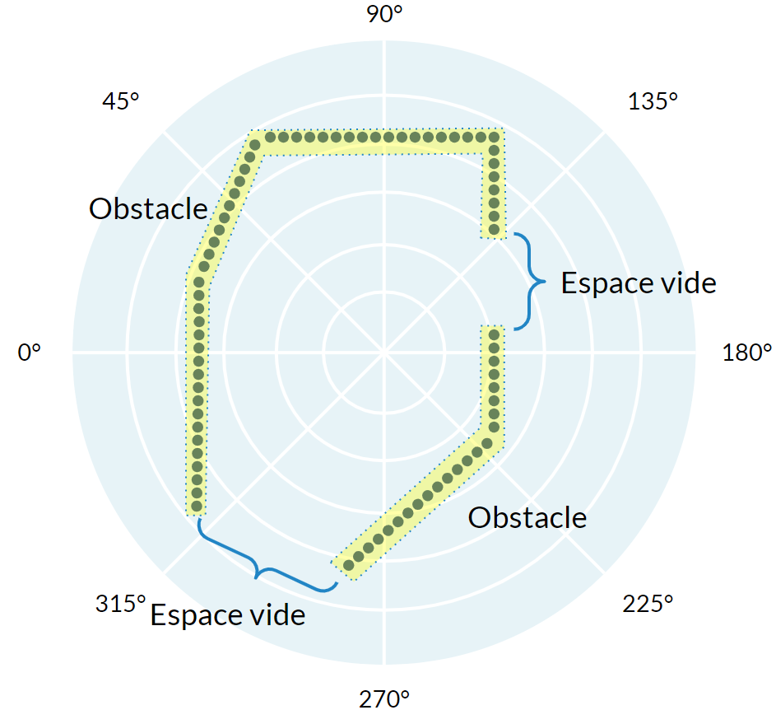
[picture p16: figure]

FIGURE 44: : REPRESENTATION DES ENSEMBLES « VIDE » ET ENSEMBLES « OBSTACLE »

(COORDONNEES CARTESIENNES)

FIGURE 45: : REPRESENTATION DES ENSEMBLES « VIDE » ET ENSEMBLES « OBSTACLE »

(CORDONNEES POLAIRES)

Sur l’ensemble de la plage de mesure on vient ainsi rassembler les points en dans un même

ensemble. Avec la capacité de différencier les espaces « vides » des ensembles

« obstacles », on peut exploiter ces espaces vides. En effet on peut déterminer le milieu de

cet ensemble vide. Ainsi comme le montre la figure suivante, selon les coordonnées du

milieu un angle se crée par rapport à la normale de la voiture.

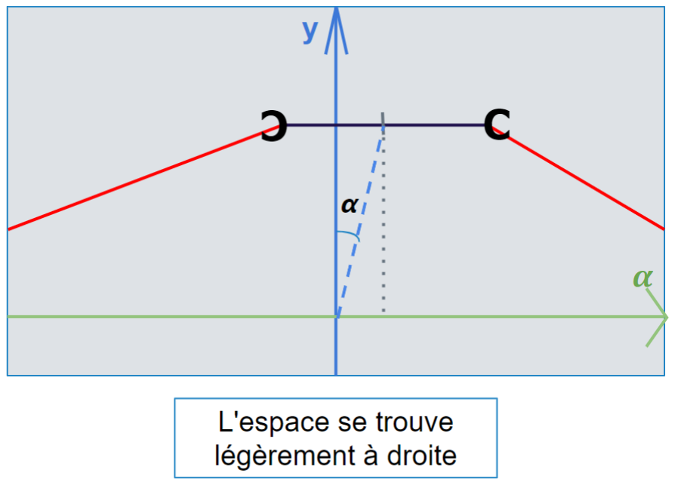
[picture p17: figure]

FIGURE 46: : ILLUSTRATIONS DE L’ALGORITHME DE DECISION DE L’ANGLE DES ROUES

Si plusieurs espaces vides se présentent, il est nécessaire de choisir le plus adapté. Pour le

choisir, on vient récupérer le nombre de points composant chaque ensemble vide pour

connaître leur taille. On se focalise donc sur l’ensemble vide le plus grand. Il est également

nécessaire de ne pas fournir un angle supérieur à l’angle de braquage des roues, de ce fait

on privilégiera un espace dont |αmilieu_ensemble| ≥ |αmax _roues| = 22°.

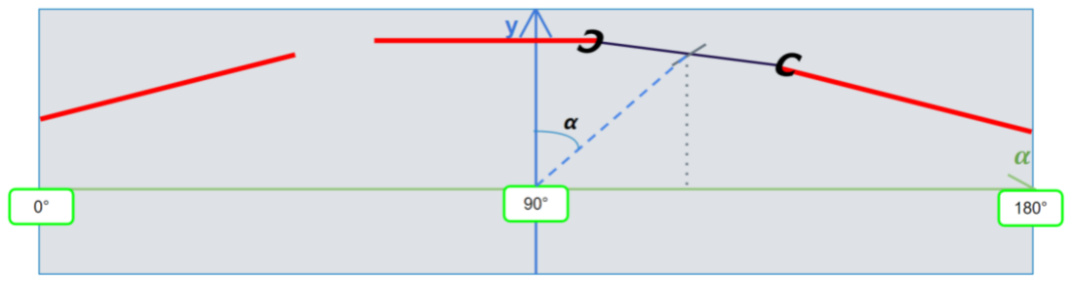
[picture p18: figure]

FIGURE 47: ILLUSTRATIONS DE L’ALGORITHME DE DECISION DE L’ANGLE DES ROUES AVEC

PLUSIEURS ENSEMBLES VIDES

Enfin pour permettre une rotation sans à-coups, c’est-à-dire sans variations brutales de

l’angle des roues, nous avons établi qu'il était nécessaire de mémoriser les valeurs d’angle

donnés précédemment afin de réaliser un filtrage. Nous pensions par exemple à un filtre à

moyenne glissante ou bien à une saturation numérique de la variation de l’angle.

## - La gestion de la vitesse

A ce stade nous n’avons pas atteint cette partie en pratique. Nous allons cependant

développer ici une approche théorique.

## 1. Accélération

Le premier des problèmes que soulève la vitesse est la notion d'accélération. Lorsque la

voiture accélère, une rotation s’effectue sur l'axe de tangage et vient perturber le

fonctionnement du LIDAR.

Conclusion : De ce fait, il faut numériquement saturer l’accélération et, probablement, la

décélération du véhicule.

## 2. Les virages

Lorsque le véhicule se déplace, celui-ci est amené à prendre des virages. Si sa vitesse est

trop élevée, une rotation s’effectue sur l’axe de lacet qui va venir effectuer un survirage (en

cas d'accélération) et un sous-virage (en cas de perte d'adhérences au niveau des roues

avant).

Conclusion : Il est donc nécessaire que la vitesse du véhicule soit fonction de l’angle des

roues, voire de la variation de l’angle des roues.

3. La vitesse maximale.

Lorsque la voiture est en ligne droite, on souhaite qu’elle accélère d’elle-même. Cependant

si la vitesse est trop élevée, nous ne pourrons anticiper les obstacles ou les virages.

Conclusion : Il est nécessaire de venir limiter la vitesse maximale de la voiture.

# Conclusion

Nous avons été capable de répondre au cahier des charges imposé par l’IUT : à savoir créer

un premier prototype de véhicule autonome. Bien que nous ayons eu des problèmes nous

avons été à même de comprendre leur origine et de trouver une solution adaptée.

A ce jour, les cartes de communication et de puissance ne sont pas terminées : elles sont en

cours d’impressions et de soudures. Les programmes de base de la voiture sont terminés :

- Avancer et tourner.
- Récupérer les données LiDAR.
- Envoyer des informations en temps réel en Bluetooth.
- Prendre des décisions en fonction des données LiDAR, infrarouge et ultrason.

Nous attendons d’assembler le tout pour vérifier le bon fonctionnement global. Nous

pourrons alors faire des tests pour mesurer le degré d’autonomie du véhicule dans un terrain

semblable à celui de la course.

Ce projet, bien qu’il ait pour objectif principal de mettre en pratique nos connaissances dans

le domaine de l'électronique, nous a aussi permis de développer nos qualités humaines et

compétences organisationnelles.

De plus il nous a permis d’utiliser le savoir acquis au semestre 3 et de développer diverses

compétences : nous avons pu travailler sur divers domaines comme l’informatique et

l’électronique embarquée, les mathématiques, la programmation en langage C++.

L’aspect humain du projet est tout aussi important et bien que certaines séances aient été

plus difficiles nous avons su nous soutenir et avancer collectivement. Les erreurs que nous

avons pu commettre lors de ce projet nous ont aussi été bénéfiques pour apprendre et

comprendre : c’est un apprentissage utile à notre avenir professionnel.

Enfin nous avons appris à travailler en autonomie avec un professeur qui a su mettre en

avant l’apprentissage autodidacte.

# Lexique

TEC : cours de traitement du signal à l’IUT de Cachan.

SA : cours de Systèmes Asservis (automatique) à l’IUT de Cachan.

CE : cours de Conversion d’Energie à l’IUT de Cachan.

IENA : cours d’informatique embarquée à l’IUT de Cachan.

Diagramme de Gantt : Un diagramme de Gantt désigne une présentation, en général un

tableau, qui permet de visualiser dans le temps les différentes tâches composants un projet.

Batterie NiMH (Nickel-hydrure métallique) : Technologie de batterie. D’autres types de

batterie existent comme les batteries au plomb. Les propriétés des batteries varient en

fonction des technologies (poids, capacité, puissance nominale).

Capteur LiDAR : Le LiDAR est une méthode de télédétection et de télémétrie semblable au

radar. Celle-ci émet des impulsions de lumière infrarouge, au lieu d'ondes radio, puis en

mesure le temps de retour après avoir été réfléchies sur des objets à proximité.

Un schéma synoptique : Présentation, en général graphique, permettant d’appréhender

l’assemblage électrique d’un système complexe.

CAO : Conception Assistée par Ordinateur. Désigne un logiciel.

CAN : Protocole de communication, qui permet de relier plusieurs systèmes entre eux afin

qu’ils communiquent sur un bus de données commun.

Carte électronique / PCB (Printed circuit board) : Support, en général une plaque,

permettant de maintenir et de relier électriquement un ensemble de composants

électroniques entre eux dans le but de réaliser un circuit électronique complexe.

I2C : Protocole de communication informatique.

Bauds : Unité de mesure de la rapidité de communication entre deux systèmes. On associe

un Baud à un « bit/secondes ». Les liaisons séries ont des standards de communications en

bauds. La valeur par défaut est de 9600 bauds. Cependant il existe d’autres vitesses de

transmission comme 115200 Bauds (requis pour communiquer avec le LiDAR).

FIFO (First In First Out) : Pour garder une continuité logique entre la transmission et la

réception des caractères il est nécessaire de conserver l’ordre. La notion de FIFO pour First

In First Out permet d’acter cette logique de traitement et d’assurer ce mode de

fonctionnement : le premier caractère envoyé, donc le premier arrivé devrait être le premier à

être traité.

Algorithme : Un algorithme est une suite finie et non ambiguë d'instructions et d’opérations

permettant de résoudre une classe de problèmes. Le domaine qui étudie les algorithmes est

appelé l'algorithmique.

FPU (Floating Point Unit) : Une unité de calcul en virgule flottante est une partie d'un

processeur, spécialement conçue pour effectuer des opérations sur des nombres à virgule

flottante. Le calcul en virgule flottante est possible avec une unité de traitement arithmétique

mais demande une centaine d’instruction machines pour réaliser un calcul.

# Annexes

## - A1 : Guide pour exploiter un répertoire GitHub

Adresse du répertoire : https://github.com/Widelx/saphteamracing.git

Afin d’accéder au travail effectué sur le LiDAR et diverses fonctions d’acquisition, nous

avons choisi d’utiliser un répertoire sur GitHub. Le lien précédent permet d’y accéder.

Une fois que vous avez accédé à celui-ci, cliquer sur Code.

FIGURE 48: UTILISER GITHUB (1)

Un menu déroulant s’affiche. Vous pouvez alors télécharger ce répertoire sur votre

ordinateur en cliquant sur Download ZIP.

FIGURE 49: UTILISER GITHUB (2)

Vous aurez alors accès à toutes les fonctions qui ont été faites. Vous pouvez bien entendu

réutiliser ce code et je vous invite vivement à utiliser Git (ou/et apprendre) pour garder votre

code propre. Vous préserverez la version la plus récente qui soit opérationnelle.

## - A2 : Utilisation d’Octave pour afficher les données LiDAR

Sur ce répertoire se trouve un dossier Octave. Celui-ci contient des scripts afin de

visualiser en liaison série ou Bluetooth ce que voit le LiDAR.

Note : Il est possible que d’ici la rédaction de ce rapport ce répertoire ai évolué et que vous

puissiez aussi voir l’angle des roues que le programme de prise de décision ordonne. Le

fichier README contient les directives à suivre pour utiliser ce script. Si une version plus à

jour que celle-ci existe je vous invite à aussi lire ce dernier en complément d’informations.

Téléchargez Octave : https://www.gnu.org/software/octave/download

- Lancez Octave et rendez-vous dans le dossier où se trouve le dossier Octave

(téléchargé depuis le répertoire) (1).

- Double-cliquez sur « App_Lidar_Viewer.m » (2).

Une fois exécuté une fenêtre s’ouvre à droite dans l’éditeur.

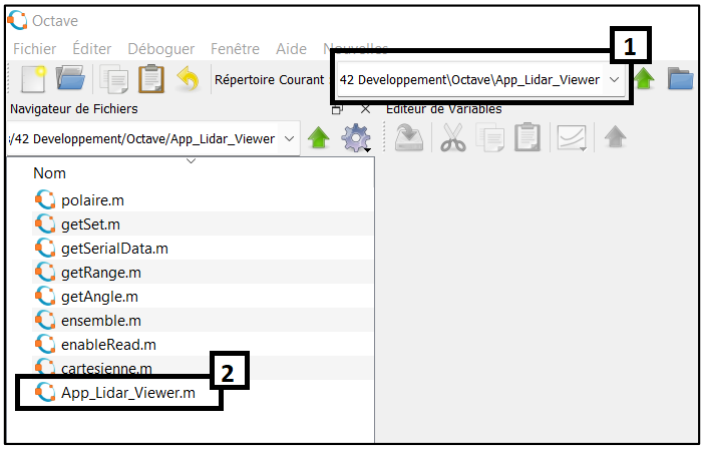
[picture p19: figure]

FIGURE 50: UTILISER OCTAVE (1)

- Connectez-vous au module Bluetooth avec votre ordinateur.
- Changez le nom « COM10 » par le numéro du port COM qui correspond (3).

Cf:

https://helpdesk.microsurvey.com/index.php?/Knowledgebase/Article/View/1345/6/

- Exécutez le script (4).

FIGURE 51: UTILISER OCTAVE (2)

Important : Pour arrêter le script il faut se rendre dans la console sur octave et faire « CTRL

+ C ». Cela arrêtera le script. Fermer la fenêtre qui affiche les points n’arrête pas le script.

Après avoir arrêté le programme il est nécessaire d’exécuter la commande « clear » dans la

fenêtre de commande.

Amélioration du programme :

Si l’envie vous prend d’éditer le code voici un tutoriel très complet d’Octave qui est aussi

disponible au format vidéo : https://www.jdbonjour.ch/cours/matlab-octave/

L’idée d’ajouter une interface de contrôle pourrait être utile : un bouton d’arrêt de la voiture,

un de démarrage, un slider de contrôle de la vitesse/accélération et quelques informations

utiles comme le nombre de points par tour ou autre.

Il est bon de savoir que sur Octave le « ; » en fin d’une ligne de commande évite que lors de

l’exécution du script, le résultat (de cette ligne) soit affiché dans la fenêtre de commande. De

plus la commande « whos » est très utile pour comprendre l’allocation mémoire dynamique.

## - B1 : Continuité des points

En mode ForceScan il arrive qu’il y ait des sauts d’angle. Cela veut dire que la stricte

croissance de l’angle n’est pas assurée. Cela n’a pas été étudié pour la fonction Scan. Ainsi

la fonction de synchronisation ne peut pas s’appuyer sur la continuité des points.

Mathématiquement la continuité de l’angle aurait sous-entendu la relation de récurrence

suivante.

Angleprécédent < Anglesuivant hormis pour le passage entre 360 et 0.

On constate que par moment, cette relation est fausse et est remplacée par la suivante :

Angleactuel < Angleprécedent < Anglesuivant

Lors de ces sauts il a été constaté que les sauts n’ont pas lieu sur plusieurs valeurs à la

suite.

## - B2 : Algorithme plus complexe

Pour pousser l’étude des algorithmes, nous proposons ici un algorithme plus

compliqué qui intègre la notion de synchronisation des trames. Celui permettrait deux

améliorations considérables :

- Modèle proche d’un fonctionnement dit « multitâche ».
- Réponse quasi immédiate de la fonction « récupérer un tour ».

Par ailleurs, sous la condition que le programme est bien écrit, celui-ci ne devrait pas

surcharger le microcontrôleur dans l’exécution de l’interruption sur RX (réception d’un octet).

Une étude complète de cette surcharge devrait tout de même être menée pour confirmer

cette hypothèse et mesurer le bénéfice réel de ce modèle. Bien entendu des connaissances

en multitâche permettrait une mise en place plus robuste d’un fonctionnement similaire.

Note : L’algorigramme (en page suivante), bien que complexe, n’est pas forcément très

explicite. Malgré l’effort pour le rendre lisible et simple, nous détaillerons ici les points de

fonctionnement qui ne seront probablement pas clair. Par ailleurs cet algorithme n’a pu être

perfectionné par manque de temps. Les fonctions les plus utiles seront détaillés mais un

réagencement de ces blocs pourrait, probablement, améliorer le modèle proposé.

- Synchronisation en temps réel

Ce modèle intègre un algorithme de synchronisation en temps réel qui permet de

vérifier la cohérence des trames. Cela assure la robustesse de l’acquisition dans le cas où

des trames auraient été perdues, ou, si l’on souhaite décoder les informations du LiDAR et

s’y synchroniser sans passer par les trames « 0xA5 0x5A » de début de transmission.

Cet algorithme pourrait déjà être utilisé pour améliorer les modèles présentés précédemment

et s’acquitter du modèle « connexion/déconnection ».

Pour analyser les trames on se base sur les éléments cités dans la sous partie

« Désynchronisation des trames ». On vérifie la cohérence sur N points. Une étude serait

nécessaire pour déterminer le nombre de trames N nécessaires pour assurer la

synchronisation.

Par ailleurs si l’analyse échoue, une fonction de reconnexion avec le LiDAR devrait être

exécutée en employant la méthode « stop/start ».

Bénéfices :

- Assure la robustesse du modèle.

- Réduit considérablement le temps de synchronisation.
- Rend la synchronisation possible à n’importe quel moment.
- Alterner le lieu de stockage

Afin de pouvoir répondre facilement à une demande du dernier tour disponible on

peut utiliser plusieurs lieux de stockage. Ainsi pendant que l’un se rempli, l’autre peut être lu.

En alternant les emplacements de stockage on peut garder le tour le plus récent et continuer

l’acquisition du tour en cours. En optimisant le stockage des points on accélère ce processus

de stockage. Cependant la partie complétion des points, que nous n’avons pas abordé, est

nécessaire uniquement si une lecture est demandée.

Le mécanisme de complétion employé ici est tel que : si un angle n’a pas été associé à une

distance lors du tour, nous recopions la distance associée à l’angle précédent. Ainsi il n’est

pas nécessaire d’effectuer ce processus si aucune lecture n’est effectuée.

Bénéfices :

- Assure d’avoir toujours le dernier tour enregistré et stocké.
- N’utilise que deux emplacements de stockage de taille minime.
- Précautions

Plusieurs précautions sont à prendre avant de se jeter sur ce type d’acquisition.

- Ce modèle repose sur un précepte essentiel : le traitement d’un même tour de façon

répétitive n’a aucun sens. Il faudrait donc s’assurer que le même tour n’est pas donné en

entrée du traitement plusieurs fois de suite.

- La synchronisation sur trame peut marcher sur le papier. Il faut cependant vérifier si cela

est faisable sans analyser un trop grand nombre de points.

- L’alternance des stockages peut poser un problème si on remet à zéro un stockage qui

est en cours de lecture. Il faut s’assurer que cela est appréhendé. On peut supposer

qu’en utilisant 3 stockages différents et que tlecture ≪ tacquisition nouveau tour cela ne

posera pas de problème.

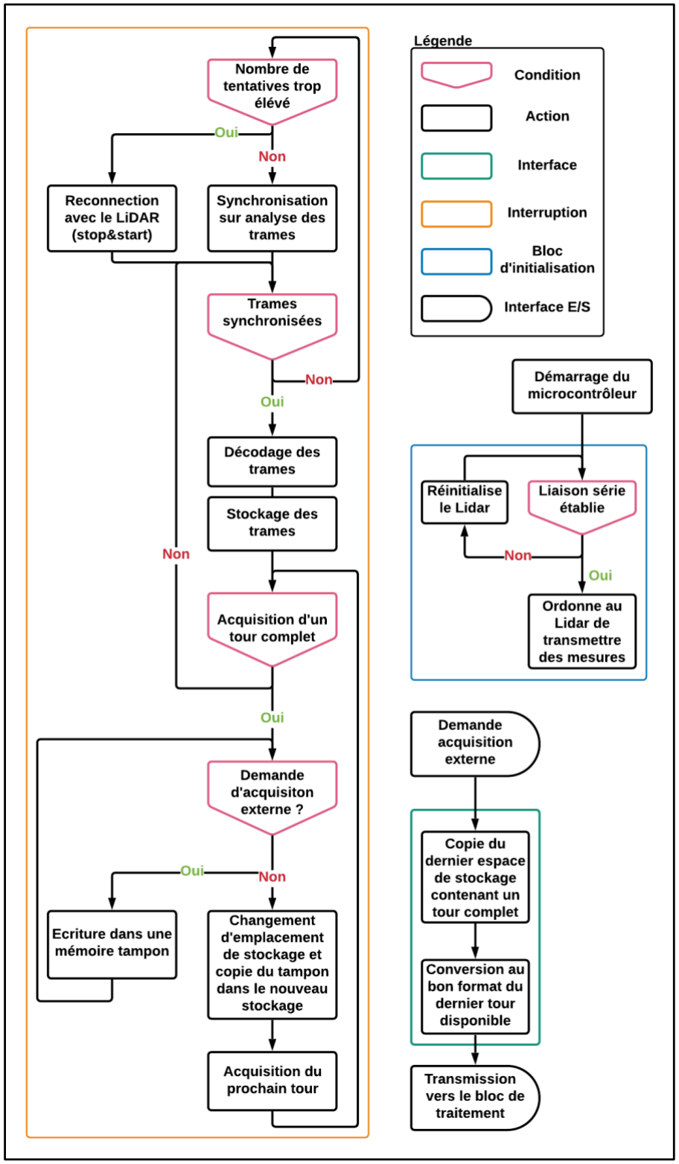
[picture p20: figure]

FIGURE 52: ALGORIGRAMME DU MODELE ANNEXE

## - C : Gestion de la direction

Pour contrôler les moteurs (servomoteur, moteur brushless) nous devons générer un

signal MLI. En effectuant des tests nous relevons les valeurs suivantes de rapports

cycliques.

FIGURE 53: EVOLUTION DES RAPPORTS CYCLIQUES

Nous allons uniquement détailler le procédé utilisé pour générer la commande du

servomoteur. Le principe étant similaire pour le moteur brushless.

Nous souhaiterions donc faire une fonction de contrôle de la direction pour laquelle nous

fournissons un angle entre -22° et 22° : un angle négatif correspondant à la gauche. Celle-ci

prend donc en argument une variable comprise entre -22 et 22° et donnant en sortie une

valeur comprise entre 0.09 et 0,063 (rapport cyclique compris entre 0 et 1 sur MBed) qui

sera appliquée sur la sortie PWM.

Sur le logiciel GéoGébra nous devons donc tracer deux points :

f(−22) = 0,09 | f(22) = 0,063

FIGURE 54: DROITE AFFINE GENERANT LE RAPPORT CYCLIQUE DU SERVOMOTEUR

Après avoir entré cette équation nous devons saturer numériquement les valeurs de l’angle

pour ne pas envoyer des signaux PWM qui seraient hors de la plage de valeurs acceptée.

Nous obtenons alors la fonction suivante en C.

Angle (degré) | -22 | 22
PWM (rapport cyclique) | 9% | 6,30%
Vitesse (absolue) | Nulle | Maximale
PWM (rapport cyclique) | 8% | 5,60%

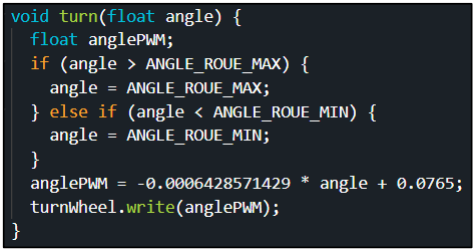
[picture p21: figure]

FIGURE 55: FONCTION EN C POUR CONTROLER LA DIRECTION

## - D : Travaux des différents étudiants

Pour transmettre notre travail, nous l’avons stocké sur un répertoire GitHub. Cela

permet de ne pas surcharger l’annexe de ce rapport avec des centaines de ligne de code.

Ainsi notre travail commun se trouve sur le répertoire GitHub suivant, dans le dossier

« Documents ». Chaque partie des étudiants se trouve dans le répertoire associé à son nom.

Pour l’élève Guillaume Dumesnil, son travail se trouve dans le reste du repository.

Par ailleurs le repository contient d’autres fichiers, comme les datasheets de tous les

composants, des modèles STL de pièces 3D, le rapport de l’équipe précédente, afin de

rendre la prise en main du projet plus simple.

Adresse du GitHub : https://github.com/Widelx/saphteamracing.git

## - E : Images annexes

FIGURE 56: PHOTO DE LA VOITURE

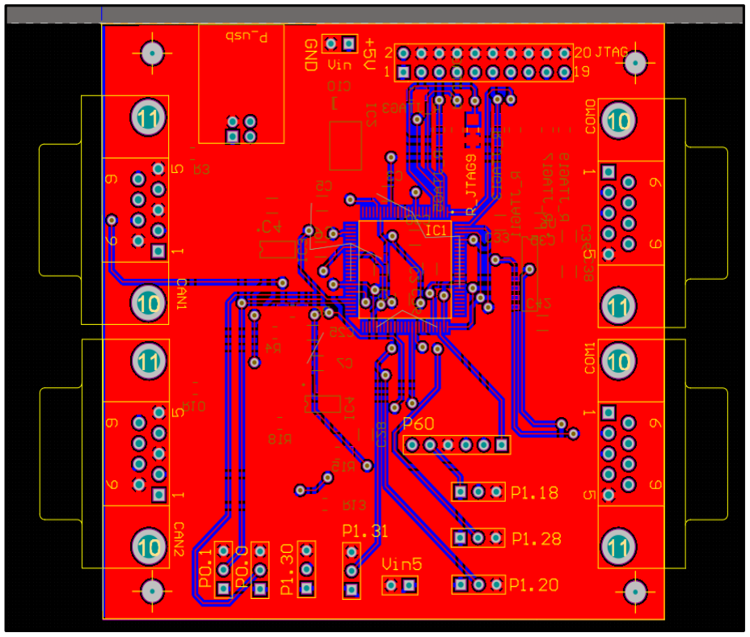
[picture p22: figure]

FIGURE 57: COUCHE SUPERIEURE DE LA CARTE PUISSANCE

FIGURE 58: COUCHE INFERIEURE DE LA CARTE PUISSANCE

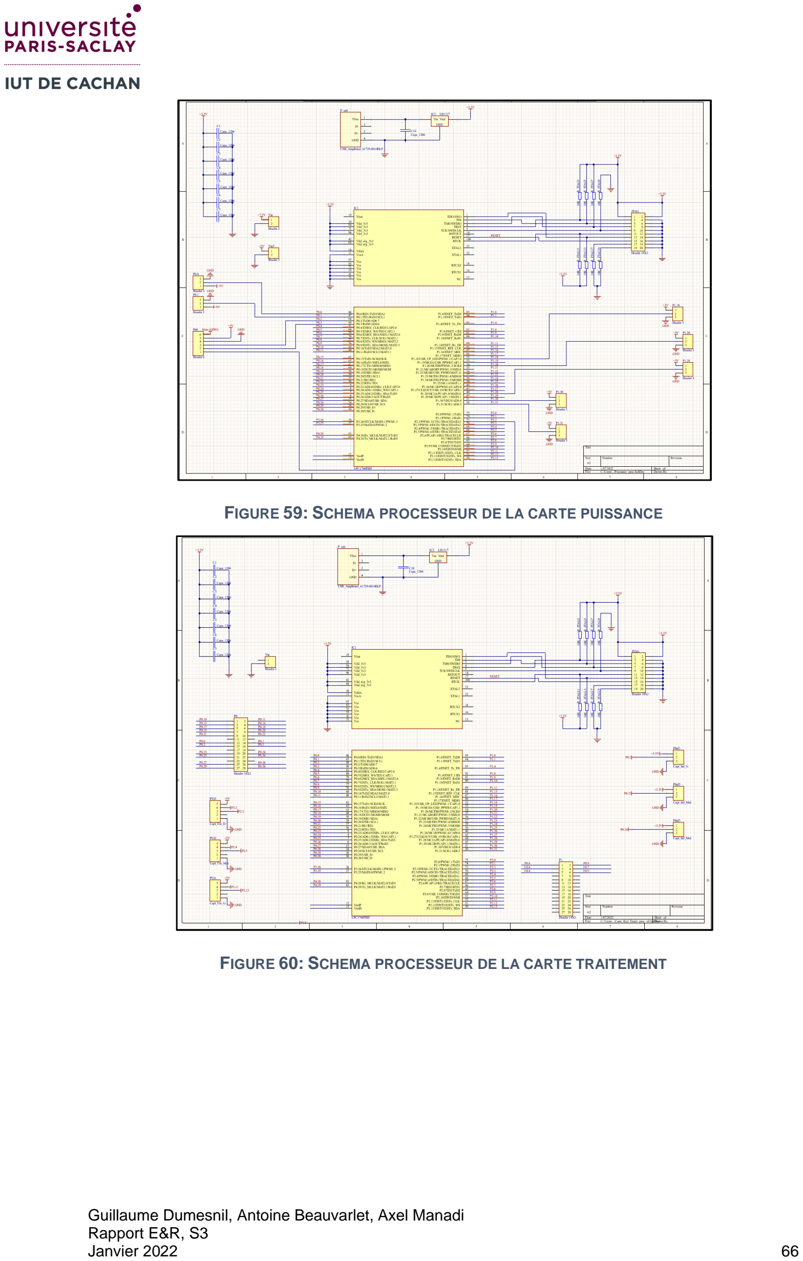
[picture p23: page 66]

FIGURE 59: SCHEMA PROCESSEUR DE LA CARTE PUISSANCE

FIGURE 60: SCHEMA PROCESSEUR DE LA CARTE TRAITEMENT

FIGURE 61: SCHEMA DE LA PARTIE CAN

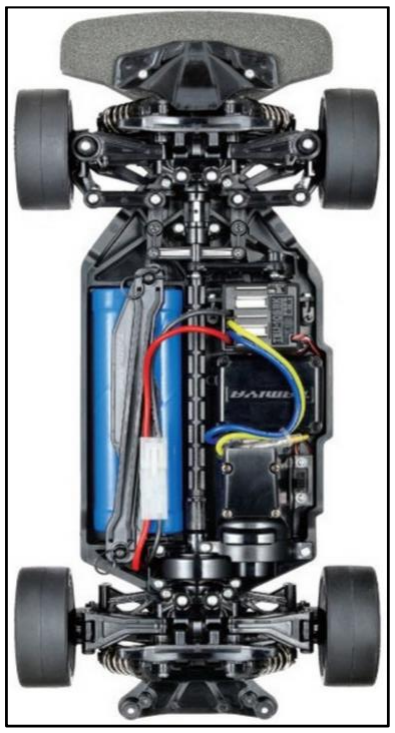
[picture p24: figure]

FIGURE 62: MAQUETTE DE LA VOITURE VUE DE DESSOUS

# Table des figures

Figure 44: : représentation des ensembles « vide » et ensembles « obstacle » (coordonnées

Figure 45: : représentation des ensembles « vide » et ensembles « obstacle » (cordonnées

Figure 47: Illustrations de l’algorithme de décision de l’angle des roues avec plusieurs

# Webographie

Diverses définitions

https://fr.wikipedia.org/wiki/Trame_(informatique)#:~:text=Dans%20les%20r%C3%A9seaux

%20informatiques%2C%20une,donn%C3%A9es)%20dans%20le%20mod%C3%A8le%20O

SI. (https://fr.wikipedia.org/wiki/Trame_(informatique))

https://fr.wikipedia.org/wiki/Baud_(mesure)

DOC LIDAR

https://www.slamtec.com/en/Support#rplidar-a-series

MBED.ORG

https://os.mbed.com/docs/mbed-os/v5.15/apis/index.html

Buffered serial

https://os.mbed.com/docs/mbed-os/v6.14/mbed-os-api-

doxy/classmbed_1_1_file_handle.html#a33b0a9b2e4f378134f6c603f28abc926 (https://os.mbed.com/docs/mbed-os/v6.14/mbed-os-api-doxy/classmbed_1_1_file_handle.html)

Serial UART

https://os.mbed.com/docs/mbed-os/v6.6/apis/serial-uart-apis.html

SITE COURSE

https://ajuton-ens.github.io/CourseVoituresAutonomesSaclay/

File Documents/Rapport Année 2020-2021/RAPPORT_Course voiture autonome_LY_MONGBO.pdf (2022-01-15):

# COURSE DE VOITURES


1

### Groupe D Créé par : Joséphine LY Karl-Emmanuel MONGBO

## EMILE MARTINCIC

# AUTONOMES

2020-2021

2

3

### REMERCIEMENTS

Nous tenons tout d’abord à remercier l’ensemble de la Direction de l’IUT de Cachan, qui nous ont permis d’intégrer l’établissement au mois de Septembre 2019.

Nous remercions notre enseignant M. MARTINCIC, qui a su nous épauler lors de ce projet, et également
M. BELLANGER qui a pu répondre à nos différentes questions.

Ensuite, nous adressons nos vifs remerciements à tout le personnel de l’IUT, pour nous avoir fourni le matériel dont nous avions besoin pour ce projet.

Nos remerciements vont enfin au corps professoral et administratif de l’IUT de Cachan pour nous avoir donné toutes les connaissances nécessaires durant ce projet.

4

### RÉSUMÉ

Depuis quelques années, nous connaissons l’avènement de la direction assistée ainsi que plusieurs aides à la conduite. Aujourd’hui, l’ère est à la voiture autonome. C’est dans cette optique que des professeurs de l’ENS Cachan ont eu l’idée d’une course de voiture autonome. Le but étant qu’à partir d’une voiture, d’un LIDAR et d’une carte programmable nous puissions construire une voiture livrée à elle-même sur un circuit. Que cette dernière puisse trouver toute seule son chemin, éviter des obstacles et être rapide.

Tels des constructeurs, nous avons les premiers jours assemblé la voiture, installé le moteur et le servomoteur. Une fois la carrosserie faite, nous devions nous interroger sur le branchement du moteur, du servomoteur, du variateur de vitesse, la gestion de la puissance, la communication avec une centrale via un module Bluetooth mais surtout, un programme de base pour faire avancer, reculer ou donner une direction à la voiture. Les tâches ont été divisées, réparties et nous étions lancés.

La batterie fournissant du 7,2V, un transformateur était indispensable pour alimenter la carte Keil, le LIDAR et le servo moteurs alimentés en 5V. Après avoir testé plusieurs transformateurs, notre professeur nous a fourni une carte qui transforme n’importe quelle tension supérieure à 6,8V en 5V. Nous avons conçu une carte d’interface qui permettait de relier les tensions de 5V et les masses entre elles, ainsi que de faire le lien entre la carte Keil que nous programmions et les différents composants qui doivent être reliés.
Au niveau de la programmation, le variateur de vitesse et le servo-moteur doivent recevoir une PWM (Modulation à Largeur d’Impulsion) qui va consigner la vitesse pour le variateur et l’angle de direction des roues avant pour le servomoteur. Le LIDAR et le module Bluetooth communiquent via une « liaison série » : notion que nous ne maîtrisions pas. Il a donc fallu apprendre à communiquer avec les liaisons séries afin d’envoyer des chaines de caractères permettant de communiquer avec le LIDAR et la centrale via le Bluetooth.

Une fois tous ces éléments développés séparément, nous devions les assembler pour tester le fonctionnement de la voiture. Nous avons donc soudé certains composants, fait les différents branchements et alimenter le tout.
Nous avions réussi à créer une voiture qui roule à partir des informations que nous lui donnons. Il ne reste plus qu’à étudier le LIDAR et les informations qu’il fournit pour rendre la voiture autonome.

Nous étions une équipe de deux pour un projet qui pouvait en demander plus. Cependant, avec une bonne organisation, de l’entraide et le soutien de notre professeur, nous ne sommes plus très loin d’avoir une voiture autonome.

Mots clés : Voiture autonome, LIDAR, Module Bluetooth, Batterie, Transformateur, Carte interface

Karl-Emmanuel
MONGBO

5

### SOMMAIRE

6

### INTRODUCTION

L’apparition des véhicules autonomes est un thème majeur de l’informatique embarquée ces dernières années. Taxis, camions, bateaux, drones, avions et même course automobile, tous les secteurs du transport sont concernés. Des premiers véhicules roulent seuls, en environnement connu ou avec un conducteur superviseur.

Une voiture dite autonome est équipée d'un système de pilotage automatique qui lui permet de circuler sans intervention humaine dans des conditions de circulation réelles.

Pour cela, le véhicule est équipé d'une série de capteurs laser (LIDAR), de radars et de caméras qui lui servent à modéliser son environnement en trois dimensions et à identifier les éléments qui le composent : marquage au sol, signalisation, bâtiments, véhicules, piétons. Afin qu'il puisse se guider en respectant les règles de circulation et éviter les obstacles.
A cela s’ajoutent des calculateurs pour le traitement des images, la fusion des données et les calculs de trajectoires.

L'ensemble de ces informations est traité par un programme d'intelligence artificielle qui décide des manœuvres à effectuer en agissant sur des servocommandes contrôlant les principales fonctions de la voiture : direction, freinage, accélération.

C’est dans ce cadre que l’ENS Paris Saclay a proposé aux étudiants en deuxième années de DUT Génie Électrique Informatique et Industrielle de participer à une course de voitures (réduites) autonomes. Le projet a commencé en octobre 2018 et s’est terminé par les courses en juin 2019. Le présent rapport vise à relater cette expérience, les choix faits par les élèves Joséphine LY, Karl-Emmanuel MONGBO et l’enseignant. Leur analyse permettra à d’autres de bénéficier de cette expérience pour entamer un projet similaire. Une nouvelle course est notamment prévue à l’ENS Paris Saclay en avril 2021.

Joséphine LY


7

### I. Présentation du défi

### 1. Le matériel fourni

En débutant ce projet nous savions que nous étions les premiers de l’IUT de Cachan à le réaliser, il n’y avait donc aucun rapport des étudiants des années précédentes pour nous guider, nous étions donc en totale autonomie et motivés pour l’entamer. Au départ nous a été fourni un châssis Tamiya TT-02, ce châssis est l’entrée de gamme pour les amateurs de course de véhicule radiocommandé mais cela ne va pas être utilisé puisque nous effectuons une voiture autonome.

Dans le kit fourni, nous y trouvons un moteur DC 540, ce moteur à courant continu se voit fonctionner à des vitesses plutôt basses. C’est alors que l’on s’est rendu compte qu’il manquait un variateur de vitesse, notre professeur nous en a alors fournit un. Lors des premières séances nous avons construit le châssis et placé le moteur ainsi que le servomoteur.

Figure 1: Le châssis construit

Notre professeur référent nous a fourni plusieurs éléments pour le bon fonctionnement du véhicule, plusieurs batteries NiMH nous ont été fournies. Avant cela nous utilisions une alimentation afin d’envoyer une tension au véhicule pour effectuer des tests tel que la programmation de la direction du véhicule. Ensuite une carte STM 32 nous a été donnée, nous avions essayé de l’utiliser mais malheureusement cette carte était inconnue pour nous. Notre choix s’est porté sur la carte LPC1768 que nous étudions depuis un certain temps, elle n’avait alors aucun secret pour nous.
Concernant la commande à distance du véhicule, un module Bluetooth RN42XVP-I/RM a été placé dans une carte interface que nous avons conçu, ce module a pour but d’effectuer les départs et les arrêts à distance du véhicule.
De plus un LIDAR RPLIDAR Slamtec A2M8 nous a été fourni, il permet de mesurer des distances en analysant les propriétés d’un faisceau lumineux qui est réfléchi vers lui-même. Ce LIDAR est l’élément central de notre projet puisque de c’est grâce à lui que le véhicule va éviter les obstacles.


8

Par ailleurs, nous avions besoin d’adapter les différentes tensions fournit par la batterie (7,2V) à la carte microcontrôleur, le LIDAR et le servomoteur (5V). Une carte d’adaptation a alors été réalisé par notre professeur, celle-ci avait pour but de remplacer le fonctionnement d’un transformateur que nous voulions utiliser au départ.

Figure 2: Le matériel fournit par le professeur

Et enfin dans le kit nous avions une carrosserie de Lancia Delta aussi semblable aux réelles voitures de course. Nous avions alors tout le matériel à disposition et nous étions parés pour débuter l’étude mécanique.

Figure 3: La carrosserie Lancia Delta fournit dans le kit

Joséphine LY


9

### 2. Le règlement

Le but est de terminer premier d’une course composé de 6 véhicules autonomes, une course avec plusieurs tours, afin de déterminer le gagnant. Chaque équipe aura un droit à l’erreur, une deuxième chance sera alors offerte à eux en cas de problèmes techniques.

Pour effectuer cette course on nous impose un cahier des charges, le véhicule doit être fabriqué à partir du kit Tamiya TT-02, de plus la carrosserie fournit doit recouvrir le véhicule à plus de 80%. Pour alimenter le véhicule il faut une batterie NiMH de 7,2V. On nous impose également d’utiliser un LIDAR comme élément central de notre véhicule.

Et enfin, l’ensemble du véhicule composé de ses capteurs et de ses actionneurs doit entrer dans les dimensions du cahier des charges, le véhicule doit avoir une hauteur inférieure à 16 cm, sa longueur doit être inférieure à 46 cm et sa largeur à 19 cm.

Afin de savoir si le véhicule peut concourir, il faut qu’il effectue une homologation pour que le jury valide le respect du cahier des charges ainsi que la vérification de l’aptitude du véhicule à se déplacer sur une piste sans toucher les bordures.

Une fois sur la piste, la communication de l’équipe avec le véhicule doit se limiter à l’envoi d’un signal de démarrage et d’un signal d’arrêt. Afin de garantir la sécurité des biens et des personnes, si la connexion entre l'équipe et le véhicule est interrompue durant plus de 2 secondes, le véhicule devra s'arrêter de manière autonome.

Le tracé de la piste n’est pas connu en avance mais elle doit avoir des bordures de 20 cm de hauteur, ces bordures devront être composées d’éléments droits et d’arcs de cercle de rayon de courbure supérieur à 50 cm, des angles droits sur les bords de pistes sont également envisageables. Il n’y aura aucun marquage au sol, la piste doit avoir une largeur supérieure à 1m et peut contenir plusieurs obstacles en plus des autres véhicules. Afin de mieux comprendre tous ces éléments voici un exemple de piste sur laquelle les véhicules pourront s’affronter.

Figure 4: Exemple de piste, dimension en cm

L’ensemble des équipes aura 3 minutes pour installer leur véhicule sur la piste, une fois que les équipes sont prêtes, il est interdit de toucher les véhicules, le signal de départ est ensuite annoncé par l’arbitre. En cas de non achèvement de la course par un véhicule, la distance parcourue par celui-ci sera calculée. Et enfin, l’arbitre a le droit de retirer un véhicule s’il trouve que celui-ci est trop agressif envers ses concurrents.

Joséphine LY

10

### II. Études et réalisations mécaniques

Une fois l’assemblage de la voiture faite, l’objectif est, dans un premier temps, de faire fonctionner le servo moteur qui va gérer la direction de la voiture et le variateur de vitesse qui gère la vitesse du véhicule.

### 1. Propulsion et direction du véhicule


Plusieurs des signaux utilisés sont des signaux de Modulation
à Largeur d’Impulsion ou PWM (Pulse With Modulation). Ces signaux ont pour caractéristiques une fréquence qui définit leur période et un rapport cyclique qui définit la duré de l’état haut du signal.


Le servo moteur utilisé est un HS-422. Il doit être alimenté en 5V (file rouge) et reçoit comme commande un signal PWM. Ce signal a une fréquence de 50Hz ce qui correspond à une période de 20 ms et un rapport cyclique variant selon l’angle de rotation souhaitée des roues. En branchant le servo moteur à un GBF (file orange), on a une déviation totale des roues à gauche pour un rapport cyclique de 6% ; une déviation nulle à 7,5% et une déviation totale à droite pour 9%.

Le variateur de vitesse utilisé est fourni avec le châssis. Sa référence est TBLE - 02s. Il est alimenté par la batterie et fait tourner un Moteur-540-Tamiya. (https://www.google.com/url?psig=AOvVaw2NzMD1h-IIk4fkavp8OwXH&cd=vfe) Ce variateur de vitesse doit être réglé en “brushless“, ce qui permet d’avoir le mode marche avant et marche arrière.
Pour cela, une fois le variateur en OFF, il faut maintenir son bouton en le mettant sur ON, relâcher, la LED clignote : rouge-vert-orange. Appuyer sur le bouton, une fois la LED sur le Vert (ce qui correspond au “brushless“ mode) réappuyer sur le bouton pour confirmer.

Figure 5: Exemple de PWM pour f=50Hz

Figure 6: Servomoteur HS-422


Figure 7: Variateur de vitesse TBLE-02S


11

La commande à envoyer au variateur est une PWM de 50Hz et donc le rapport cyclique définit la vitesse des roues. Afin de connaître la valeur du rapport cyclique à imposer, des mesures ont été faites à partir d’une PWM envoyée par un GBF. Pour différentes valeurs du rapport cyclique, nous avons relevé la vitesse des roues et obtenu la courbe suivante. On constate que :
- la vitesse varie linéairement en fonction du rapport cyclique,
- la vitesse max est atteinte pour 5.6%
- la vitesse nulle entre 7.5% et 8.1% et on a la marche arrière max à 9.2%.

### 2. Le LIDAR et le module Bluetooth

Deux éléments : le LIDAR et le module Bluetooth communiquent avec le µC a travers une liaison série : les UART (Universal Asynchronous Receiver Transmitter : émetteur-récepteur asynchrone universel). L’UART est un dispositif matériel informatique pour la communication série asynchrone dans lequel le format de données et les vitesses de transmission sont configurables. Il envoie des bits de données un par un, du moins significatif au plus significatif, encadrés par des bits de début et d’arrêt afin que le timing précis soit géré par le canal de communication. Pour ce faire, il utilise principalement 2 ports : TX pour la transmission d’information et RX pour la réception.

La documentation du LIDAR RPLIDAR A3, fournit les informations à lui transmettre sur ses ports :

Figure 9: ports d’alimentation et de commande du LIDAR Figure 10: définition des signaux des ports du LIDAR

Il est alimenté en 5V, reçoit un signal PWM (de 25kHz et 60% de rapport cyclique) qui règle sa vitesse de rotation et communique avec le microcontrôleur à partir de deux ports TX pour la transmission d’informations et RX pour la réception.

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
5 | 6 | 7 | 8 | 9 | 10

vitesse en fonction du rapport cyclique de la PWM

Figure 8: Variation de la vitesse en fonction du rapport cyclique

12


Concernant le module Bluetooth, il s’agit d’un RN42XVP-I/RM. Il est à plusieurs ports mais nous n’allons nous intéresser qu’à cinq ports : les 3.3V et la masse pour l’alimenter, CTS pour le statut (connecté ou non), TXD et RXD pour la transmission et la réception d’information.

### 3. Mesure de vitesse

Afin d’asservir la vitesse et de ne pas négliger les possibles aléas qui feront modifier la vitesse réelle de la voiture, notamment un blocage des roues lors d’un choc contre un obstacle, nous avons prévu d’ajouter un capteur optique : un OPB704WZ qui une fois câblé avec ses quatre ports, va renseigner sur la vitesse réelle des roues grâce à une point blanc sur l’arbre de transmission.. Pour cela, une petite tache blanche a été faite sur la roue : le capteur détectant le nombre de fois qu’il a vu cette tache, ce qui correspond à la vitesse des roues.

Karl-Emmanuel
MONGBO

Figure 12: module Bluetooth
RN42XVP-I/RM | Figure 11: ports du module Bluetooth


13

### III. Conception et réalisation électronique

### 1. Le capteur optique de mesure de vitesse

En plus du LIDAR, la voiture utilisera un capteur optique, nous avons choisi d’utiliser un OPB704WZ :

Figure 13: capteur optique OPB704WZ

Ce capteur est l’association d’un phototransistor et d’une diode électroluminescente infrarouge. C’est un capteur réfléchissant utilisé pour détecter la présence ou l'absence d'objet, ou mesurer la distance par rapport à ces objets. Dans ce capteur, la diode est associée à une résistance de 220 Ω pour maitriser le courant entrant dans la diode. Le transistor lui, est associé à une résistance de 20k Ω. Cette résistance est nécessaire pour les deux phases suivantes :

− Lors du passage du capteur optique sur du blanc, ce qui va assurer la saturation du transistor ; − Lors du passage du capteur optique sur du noir, ce qui va bloquer le transistor.

Figure 14: Montage électronique du capteur de mesure de vitesse d’arbre


14

On a par la suite effectué des tests pour savoir si ce capteur optique fonctionne et si c’était celui qu’il nous fallait. On a alors effectué les branchements sur la plaque Labdec puis alimenté le tout. On a ensuite passé le capteur optique sur une ligne blanche et nous avons observé le comportement du capteur avec un oscilloscope. Nous avons remarqué que lorsque le capteur passait sur une ligne blanche, un changement d’amplitude se manifesté au niveau de l’oscilloscope. Suite à cela, nous avons approuvé le fonctionnement du capteur optique OPB704WZ.

Figure 15: Test du capteur optique OPB704WZ sur la plaque Labdec

Concernant la localisation du capteur optique sur le véhicule, il sera placé à la hauteur d’une roue afin qu’il puisse mesurer la vitesse du véhicule, si ce dernier est à l’arrêt cela va permettre au véhicule d’effectuer une marche arrière.

Joséphine LY


15

### 2. La carte d’interface

La carte d’interface a été réalisée afin d’effectuer le lien entre la carte microcontrôleur LPC1768 et les différents composants (comme par exemple le module Bluetooth). Ce dernier a pour but d’effectuer les départs et arrêts à distance du véhicule.

La carte d’interface a été conçue sous le logiciel Altium Designer, ce dernier est composé de différentes bibliothèques regroupant de nombreux composants déjà créés telle qu’une résistance. La conception de cette carte nous a parue plutôt simple car peu de composant à mettre dessus. En revanche, la tâche s’est avérée plus difficile au niveau des bibliothèques car le module Bluetooth n’a jamais été créé.

Apprendre à créer une nouvelle bibliothèque pour un composant était nécessaire sur ce logiciel, en voici les étapes :

Dans un premier temps, nous recherchons la datasheet (fiche technique) du composant, puis on essaye de trouver ses mensurations. On crée alors la nouvelle bibliothèque, celle-ci est composée du schéma et de l’empreinte du composant, le schéma servira lors du placement du composant sur la carte avec l’ensemble des autres composants. L’empreinte sera utile pour avoir les mensurations identiques au composant. Lors de la création du schéma, on place le nombre de broche nécessaire ainsi que les noms de ces dernières, l’emplacement des broches est important car si on se trompe de sens lors du soudage, le composant ne sera pas dans le bon sens.

Figure 16: Schéma du module Bluetooth sur Altium Designer

Une fois le schéma créé, on passe à la création de l’empreinte du composant, il faut faire attention aux mesures indiquées dans les datasheets puisque celles-ci sont souvent en anglais puis il faut également les convertir en millimètre et enfin, en mil qui est l’unité utilisée sur Altium.


16

Figure 17: Empreinte du module Bluetooth sur Altium Designer

Une fois la bibliothèque compilée et intégrée dans le projet de la carte d’interface, on peut placer le nouveau composant sur la carte.

La carte est composée de connecteurs, de diodes, de résistances ainsi que du module Bluetooth, nous avions ensuite routé le PCB de la carte et nous l’avions envoyé à notre professeur pour qu’il vérifie notre création avant son impression.

Figure 18: Schéma de la carte interface


17

Figure 19: PCB et routage de la carte interface

Voici le résultat final de la carte imprimée puis soudée avec l’ensemble des composants.

Figure 20: Carte interface avec l’ensemble des composants soudés

Une fois les éléments soudés, nous avions constaté qu’une inversion des connections du module Bluetooth a été réalisée. Nous savons dorénavant qu’il faut porter une attention particulière lorsque l’on connecte les différents composants lors de la création de la carte. Refaire une nouvelle carte n’a pas été nécessaire car une solution a été trouvée avec l’aide de notre professeur, en gardant la carte initialement réalisée.

Figure 21: Correction du branchement du module Bluetooth sur la Bottom layer

Pour nos successeurs, voici le branchement que nous aurions dû réaliser.


18

Figure 22: Schéma rectifié de la carte d’interface

Une fois les éléments mécaniques réalisés, nous étions parés pour la programmation du véhicule.

Joséphine LY

19

### IV. Informatique
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

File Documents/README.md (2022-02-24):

#Description

Ce dossier contient toutes les informations et le reste du travail fourni par l'équipe lors du projet SaphTeamRacing, course de voiture autonomes.  
Ce dossier contient le travail des 3 étudiants suivants sur le semestre 3 de 2021/22 :
- Guillaume de Maricourt
- Axel Manadi
- Antoine Beauvarler

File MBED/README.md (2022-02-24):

# Prise en main

Librairies développées à l'IUT de Cachan pour MBED OS v5.15 en C++ (issu de connaissances en C et non de C++).  
Développée par Guillaume de Maricourt en 2021/22 sur le projet SaphTeamRacing, course de voiture autonomes.  

**⚠️ Utiliser la librairie SaphTeamRacing_Librairie** : l'autre dossier traite de l'algorithme vu en annexe du rapport mais n'est pas une version stable.  
⚠️ Pour voir un exemple d'un programme utilisant correctement la librairie veuillez vous référer au fichier `main.cpp`.  

### Lidar
La librairie "lidar" permet d'utiliser un capteur LiDAR de la marque SLAMTEC en récupérant un jeu de données au degré prêt dans un tableau fourni par l'utilisateur.  
**⚠️ ATTENTION :** le tableau fourni par l'utilisateur doit ABSOLUMENT être de type `float` et de taille 181 (ici tab).

Il faut pour bénéficier de cette fonctionnalité ajouter les fonctions suivantes.
```
initLidar();
getLidarData(tab);
```
Il faut bien entendu ajouter les fichier `lidar.cpp` et `lidar.h` dans le dossier du programme `main.cpp` et les inclure dans le projet.  
Certaines propriétées peuvent être directement modifiées dans le ficher .h, comme le rapport cyclique du PWM ou la distance maximale d'acquisition.

### BLE (Bluetooth Low Energy)  
Par ailleurs les données du LiDAR peuvent être visualisées via une connection série. Celle-ci peut être :
- bluetooth
- filaire  

La librairie "bluetooth" permet d'utiliser cette fonctionnalité en parrallèle avec un [script](https://github.com/Widelx/saphteamracing/tree/main/Octave) réalisé sur [Octave](https://www.gnu.org/software/octave/index)(6.3.0) _(disponible dans ce repoistory)_.

**⚠️ ATTENTION :** le tableau fourni par l'utilisateur doit ABSOLUMENT être de type `float` et de taille 181 (ici tab).  
Il faut pour bénéficier de cette fonctionnalité ajouter les fonctions suivantes.
```
initBLE();
sendOverBluetooth(tab);
```
Il faut bien entendu ajouter les fichier `bluetooth.cpp` et `bluetooth.h` dans le dossier du programme `main.cpp` et les inclure dans le projet.

Comment utiliser les deux types liaisons :
1. Liaison filaire  

La librairie est configurée de base pour transmettre en liaison filaire. Il ne devrait pas y avoir à faire ces modificcations. 

Cependant si un problème subsiste veuillez effectuer les étapes suivantes.
Modifier dans le fichier `bluetooth.h` les valeurs de `TXBLE` et `RXBLE` par les valeurs des pins à utiliser (dans notre cas `USBRX` et `USBTX`)
```
#define RXBLE USBRX
#define TXBLE USBTX
```

2. Liaison Bluetooth  

La librairie n'est pas configurée de base pour émettre en bluetooth. Il faut pour cela connecter un module qui peut communiquer en RS232 et à 115200 bauds.  
Il faut modifier dans le fichier `bluetooth.h` les valeurs de `TXBLE` et `RXBLE` par les valeurs des pins connectés sur le module bluetooth.
```
#define RXBLE PA_0
#define TXBLE PA_1
```

##### Visualisation des données en Bluetooth  
Veuillez vous référer à la section [Octave](https://github.com/Widelx/saphteamracing/tree/main/Octave) de ce git.
Bluetooth

### Car
La librairie "car" permet de contrôler la voiture. Les fichiers ".h" permettent de configurer les PINs de contrôle des signaux PWM.

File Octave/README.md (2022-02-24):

# Prise en main

Script réalisé à l'IUT de Cachan pour Octave 6.3.0.  
Développée par Guillaume de Maricourt en 2021/22 sur le projet SaphTeamRacing, course de voiture autonomes.  

Ce programme écrit pour Octave permet de visualiser les données collectées par le LiDAR (voir le dossier [MBED](https://github.com/Widelx/saphteamracing/tree/main/MBED)).

### Guide Windows
1. Trouver le bon port COM
  
Il faut aller dans les périphériques connectés pour connaitre le port COM utilisé par votre PC pour la communication avec le module bluetooth.
Le programme est à lancer en remplaçant la valeur du port COM sur lequel est connecté le module bluetooth par le port réel.
```
portCom = "COM10"; (par défaut)
portCom = "COM25";
```
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

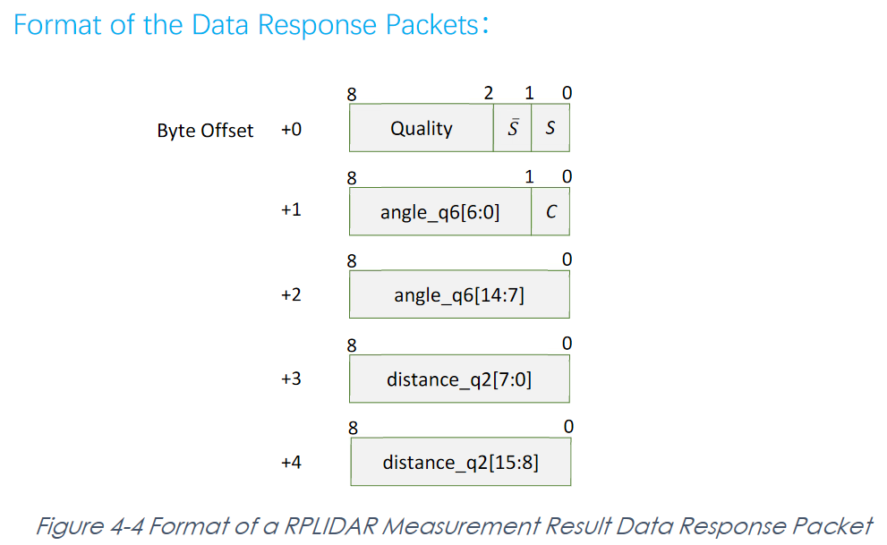
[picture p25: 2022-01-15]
Documents/Datasheets/Lidar/Lidar - format reponses (1).PNG

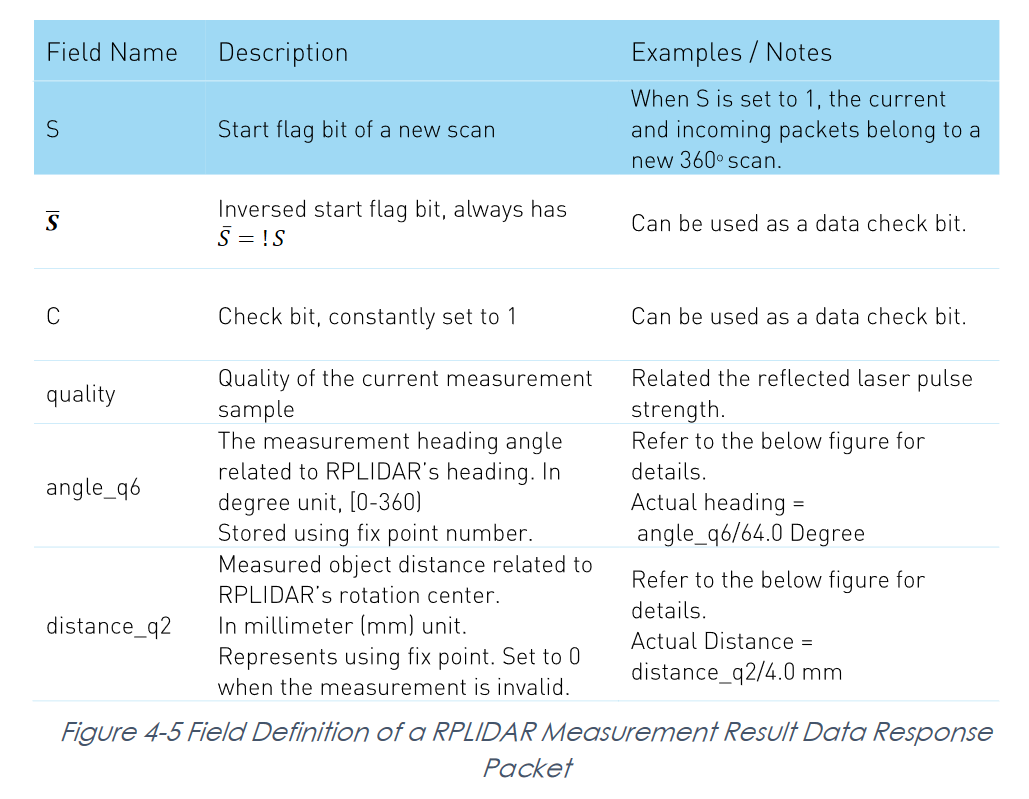
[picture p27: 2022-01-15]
Documents/Datasheets/Lidar/Lidar - format reponses (2).PNG

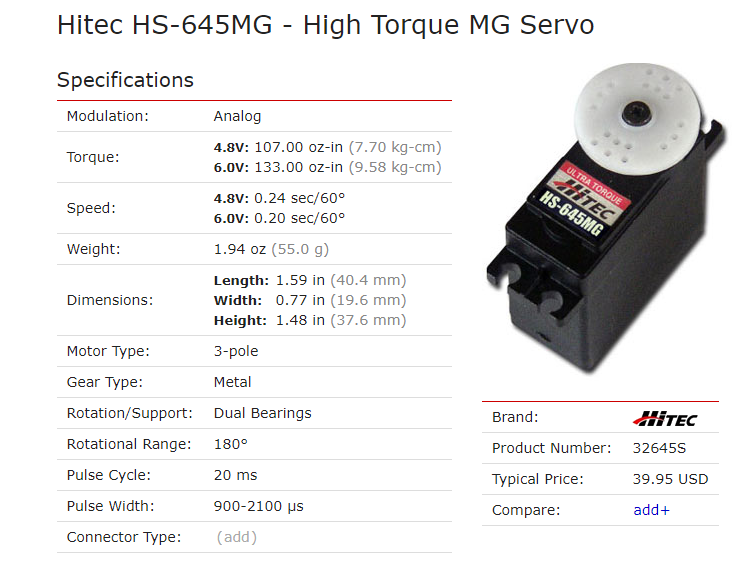
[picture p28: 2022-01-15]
Documents/Datasheets/Servo moteur Hitec.PNG

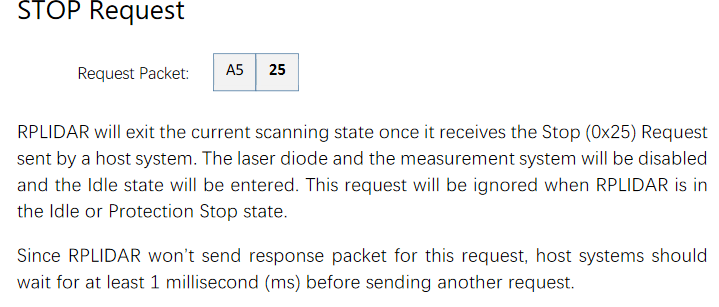
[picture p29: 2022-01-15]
Documents/Datasheets/Lidar/Lidar - Stop request info.PNG

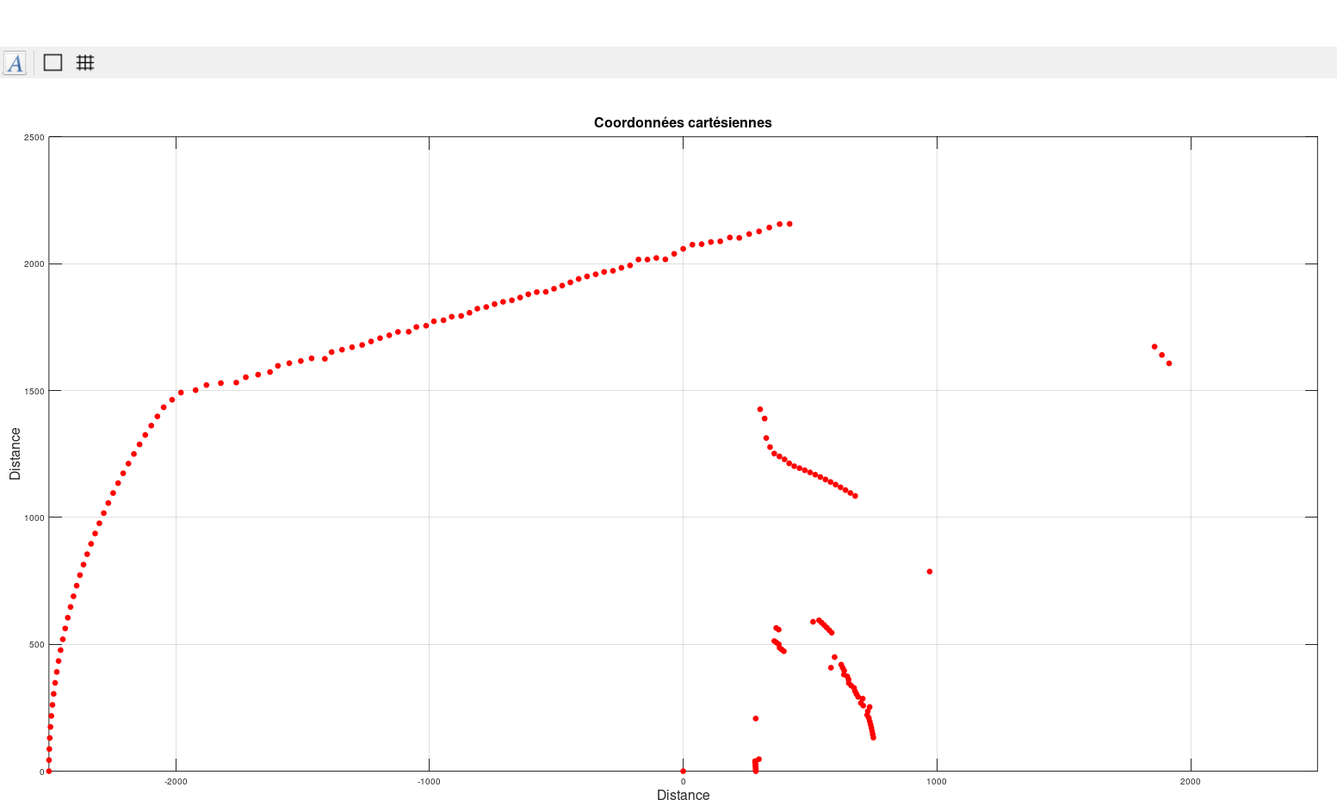
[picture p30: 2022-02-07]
Octave/Images outils/BLE (2).png

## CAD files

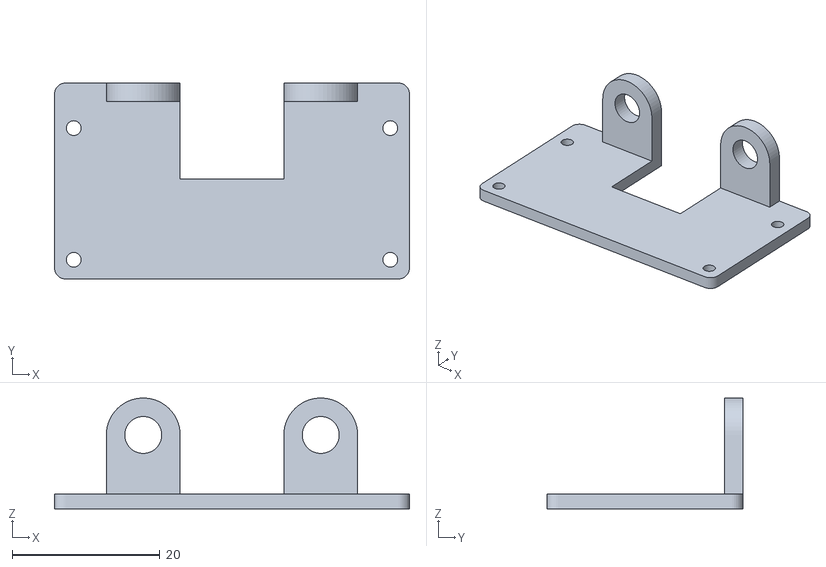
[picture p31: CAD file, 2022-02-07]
Documents/Pièces 3D/SRF04.stl
48.0 x 26.5 x 15.0

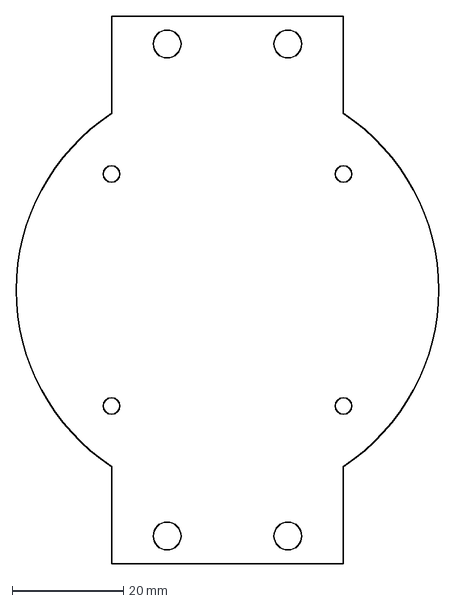
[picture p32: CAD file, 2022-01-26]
Documents/Plaque de fixation en bois/plaque_lidar.dxf
76.0 x 98.5 mm

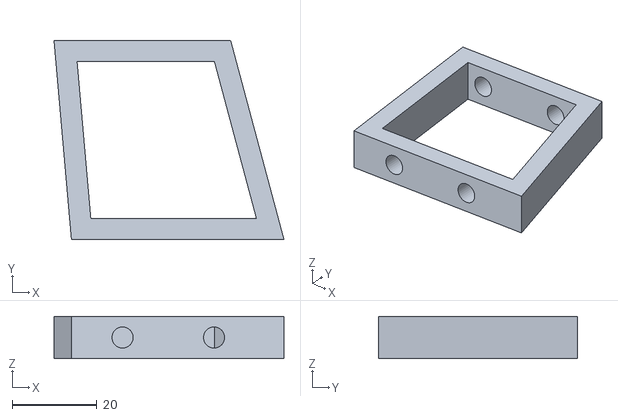
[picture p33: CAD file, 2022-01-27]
Documents/Pièces 3D/Armature_lidar.stl
54.3 x 47.0 x 10.0

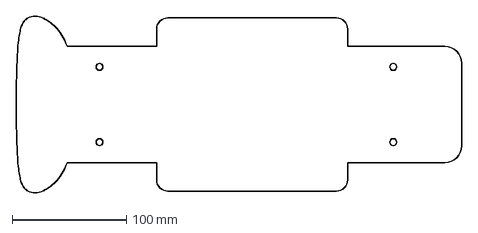
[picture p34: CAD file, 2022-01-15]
Documents/Plaque de fixation en bois/plaque_chassis.dxf
390.5 x 154.8 mm

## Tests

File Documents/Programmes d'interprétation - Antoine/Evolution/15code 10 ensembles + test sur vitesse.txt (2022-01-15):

#include <sys/stat.h>
#include <stdio.h>
#include <stdlib.h>
#include <math.h>
#define taille 181

struct Ensemble{
float debut;
float fin;
    int vide;

float angle_debut;
float angle_fin;

    float distance_debut;
float distance_fin;
float size;

};

const char* filename = "input.txt";
float lissage(float tab[taille]);
float choix_angle(int cs,float tab[taille],struct Ensemble e1, struct Ensemble e2, struct Ensemble e3, struct Ensemble e4, struct Ensemble e5, struct Ensemble e6 , struct Ensemble e7, struct Ensemble e8, struct Ensemble e9, struct Ensemble e10);

int main(int argc, char *argv[])
{
    struct Ensemble e1 = {0,0,0};
    struct Ensemble e2 = {0,0,0};
    struct Ensemble e3 = {0,0,0};
    struct Ensemble e4 = {0,0,0};
    struct Ensemble e5 = {0,0,0};
    struct Ensemble e6 = {0,0,0};
    struct Ensemble e7 = {0,0,0};
    struct Ensemble e8 = {0,0,0};
    struct Ensemble e9 = {0,0,0};
    struct Ensemble e10 = {0,0,0};

    int i,o;
    char cs=0;
    float valeur = 0, angle_roues, vitesse;   // Vmax-0.5*ln(|x|)-0.01*exp(|x|)

    float tab[taille];

    int u=0;

//--------------------------------------------------------------                recuperation donées fichier texte
    FILE *in_file = fopen(filename, "r");

    struct stat sb;
    stat(filename, &sb);

    char *file_contents = malloc(sb.st_size);

        while (fscanf(in_file, "%[^\n] ", file_contents) != EOF)
            {

            tab[u] =  atof(file_contents);
            u++;
            }

    fclose(in_file);
//--------------------------------------------------------------

for(o=0;o!=80;o++)//while(1)
    {
    lissage(tab);

    for(i=1; i!=taille+1; i++)
        {
            valeur =((tab[i])/(tab[i+1]));

            e1.debut = 0;
            e1.angle_debut = 1;
            e1.distance_debut = tab[1];

            switch(cs){

            case 0:{
                if (!((valeur<1.05)&&(valeur>0.95))){

                    e1.fin = i;
                    e1.angle_fin = i;
                    e1.distance_fin = tab[i];

                    e2.debut = i+1;
                    e2.angle_debut = i+1;
                    e2.distance_debut = tab[i+1];

                    cs = 1;}
                break;}

            case 1:{
                if (!((valeur<1.05)&&(valeur>0.95))){

                    e2.fin = i;
                    e2.angle_fin = i;
                    e2.distance_fin = tab[i];

                    e3.debut = i+1;
                    e3.angle_debut = i+1;
                    e3.distance_debut = tab[i+1];

                    cs = 2;}
                break;}

            case 2:{
                if (!((valeur<1.05)&&(valeur>0.95))){

                    e3.fin = i;
                    e3.angle_fin = i;
                    e3.distance_fin = tab[i];
                if(i<179)
                        {
                    e4.debut = i+1;
                    e4.angle_debut = i+1;
                    e4.distance_debut = tab[i+1];

                    cs = 3;}}
                break;}

            case 3:{
                if (!((valeur<1.05)&&(valeur>0.95))){

                    e4.fin = i;
                    e4.angle_fin = i;
                    e4.distance_fin = tab[i];
                if(i<179)
                        {
                    e5.debut = i+1;
                    e5.angle_debut = i+1;
                    e5.distance_debut = tab[i+1];

                    cs = 4;}}
                break;}

            case 4:{
                if(!((valeur<1.05)&&(valeur>0.95))){

                    e5.fin = i;
                    e5.angle_fin = i;
                    e5.distance_fin = tab[i];
                if(i<179)
                        {
                    e6.debut = i+1;
                    e6.angle_debut = i+1;
                    e6.distance_debut = tab[i+1];

                    cs = 5;}}
                break;}

            case 5:{
               if(!((valeur<1.05)&&(valeur>0.95))){

                    e6.fin = i;
                    e6.angle_fin = i;
                    e6.distance_fin = tab[i];
                if(i<179)
                        {
                    e7.debut = i+1;
                    e7.angle_debut = i+1;
                    e7.distance_debut = tab[i+1];

                    cs = 6;}}
                break;}

            case 6:{
               if(!((valeur<1.05)&&(valeur>0.95))){

                    e7.fin = i;
                    e7.angle_fin = i;
                    e7.distance_fin = tab[i];
                if(i<179)
                        {
                    e8.debut = i+1;
                    e8.angle_debut = i+1;
                    e8.distance_debut = tab[i+1];

                    cs = 7;}}
                break;}

            case 7:{
               if(!((valeur<1.05)&&(valeur>0.95))){

                    e8.fin = i;
                    e8.angle_fin = i;
                    e8.distance_fin = tab[i];
                if(i<179)
                        {
                    e9.debut = i+1;
                    e9.angle_debut = i+1;
                    e9.distance_debut = tab[i+1];

                    cs = 8;}}
                break;}

            case 8:{
               if(!((valeur<1.05)&&(valeur>0.95))){

                    e9.fin = i;
                    e9.angle_fin = i;
                    e9.distance_fin = tab[i];

                if(i<179)
                        {
                    e10.debut = i+1;
                    e10.angle_debut = i+1;
                    e10.distance_debut = tab[i+1];

                    cs = 9;}}
                break;}

            case 9:{
               if(!((valeur<1.05)&&(valeur>0.95))){

                    e10.fin = i;
                    e10.angle_fin = i;
                    e10.distance_fin = tab[i];

                break;}}
            }

    }//fin for(i=1; i!=taille+1; i++)

    angle_roues = choix_angle(cs,tab,e1, e2, e3, e4, e5 ,e6,e7,e8,e9,e10);
    printf("angle_roues = %lf\t",angle_roues);

    cs = 0;

for(i=2; i!=taille+1; i++){tab[i]=tab[i+1];} //decalage du passage vers la droite

if (angle_roues> 40){vitesse = 0;}
else{
if (angle_roues< -40){vitesse = 0;}
else {
       if (angle_roues >= 0) vitesse = 100-angle_roues;
       else vitesse = 100 + angle_roues;
       }

}

printf("vitesse = %lf\n\n",vitesse);
    }//fin while

return 0;

} //fin main

float lissage(float tab[taille])
{

    int i;
    float valeur2;

    tab[i]=tab[i] * (asin ( i ));  //projection

    for(i=1; i!=taille; i++)  //lissage
        {
        if (i >=1)
            {
            valeur2 = ((tab[i-1])/(tab[i+1]));
            if (((valeur2<1.05)&&(valeur2>0.95))) {tab[i] = ((tab[i-1])+(tab[i+1]))/2.0; }
            }
        }
}

float choix_angle(int cs,float tab[taille],struct Ensemble e1, struct Ensemble e2, struct Ensemble e3, struct Ensemble e4, struct Ensemble e5, struct Ensemble e6 , struct Ensemble e7, struct Ensemble e8, struct Ensemble e9, struct Ensemble e10)
{
    int e1_vide = 0,e2_vide = 0,e3_vide = 0,e4_vide = 0,e5_vide = 0,e6_vide = 0,e7_vide = 0,e8_vide = 0,e9_vide = 0,e10_vide = 0;
    int a=0,i;
    float result;
    cs +=1;

    switch(cs)
        {
         case 1:
            {
            if(tab[(int)((e1.angle_fin-e1.angle_debut)/2.0+e1.angle_debut)] == -1){e1_vide = 1;e1.vide = 1;}
            e1_vide *= (e1.angle_fin-e1.angle_debut);
            break;
            }
         case 2:
            {
            if(tab[(int)((e1.angle_fin-e1.angle_debut)/2.0+e1.angle_debut)] == -1){e1_vide = 1;e1.vide = 1;}
            if(tab[(int)((e2.angle_fin-e2.angle_debut)/2.0+e2.angle_debut)] == -1){e2_vide = 1;e2.vide = 1;}

            e1_vide *= (e1.angle_fin-e1.angle_debut);
            e2_vide *= (e2.angle_fin-e2.angle_debut);

            break;
            }
         case 3:
            {
            if(tab[(int)((e1.angle_fin-e1.angle_debut)/2.0+e1.angle_debut)] == -1){e1_vide = 1;e1.vide = 1;}
            if(tab[(int)((e2.angle_fin-e2.angle_debut)/2.0+e2.angle_debut)] == -1){e2_vide = 1;e2.vide = 1;}
            if(tab[(int)((e3.angle_fin-e3.angle_debut)/2.0+e3.angle_debut)] == -1){e3_vide = 1;e3.vide = 1;}

            e1_vide *= (e1.angle_fin-e1.angle_debut);
            e2_vide *= (e2.angle_fin-e2.angle_debut);
            e3_vide *= (e3.angle_fin-e3.angle_debut);

            break;
            }
         case 4:
            {
            if(tab[(int)((e1.angle_fin-e1.angle_debut)/2.0+e1.angle_debut)] == -1){e1_vide = 1;e1.vide = 1;}
            if(tab[(int)((e2.angle_fin-e2.angle_debut)/2.0+e2.angle_debut)] == -1){e2_vide = 1;e2.vide = 1;}
            if(tab[(int)((e3.angle_fin-e3.angle_debut)/2.0+e3.angle_debut)] == -1){e3_vide = 1;e3.vide = 1;}
            if(tab[(int)((e4.angle_fin-e4.angle_debut)/2.0+e4.angle_debut)] == -1){e4_vide = 1;e4.vide = 1;}

            e1_vide *= (e1.angle_fin-e1.angle_debut);
            e2_vide *= (e2.angle_fin-e2.angle_debut);
            e3_vide *= (e3.angle_fin-e3.angle_debut);
            e4_vide *= (e4.angle_fin-e4.angle_debut);

            break;
            }
         case 5:
            {
            if(tab[(int)((e1.angle_fin-e1.angle_debut)/2.0+e1.angle_debut)] == -1){e1_vide = 1;e1.vide = 1;}
            if(tab[(int)((e2.angle_fin-e2.angle_debut)/2.0+e2.angle_debut)] == -1){e2_vide = 1;e2.vide = 1;}
            if(tab[(int)((e3.angle_fin-e3.angle_debut)/2.0+e3.angle_debut)] == -1){e3_vide = 1;e3.vide = 1;}
            if(tab[(int)((e4.angle_fin-e4.angle_debut)/2.0+e4.angle_debut)] == -1){e4_vide = 1;e4.vide = 1;}
            if(tab[(int)((e5.angle_fin-e5.angle_debut)/2.0+e5.angle_debut)] == -1){e5_vide = 1;e5.vide = 1;}

            e1_vide *= (e1.angle_fin-e1.angle_debut);
            e2_vide *= (e2.angle_fin-e2.angle_debut);
            e3_vide *= (e3.angle_fin-e3.angle_debut);
            e4_vide *= (e4.angle_fin-e4.angle_debut);
            e5_vide *= (e5.angle_fin-e5.angle_debut);

            break;
            }
         case 6:
            {
            if(tab[(int)((e1.angle_fin-e1.angle_debut)/2.0+e1.angle_debut)] == -1){e1_vide = 1;e1.vide = 1;}
            if(tab[(int)((e2.angle_fin-e2.angle_debut)/2.0+e2.angle_debut)] == -1){e2_vide = 1;e2.vide = 1;}
            if(tab[(int)((e3.angle_fin-e3.angle_debut)/2.0+e3.angle_debut)] == -1){e3_vide = 1;e3.vide = 1;}
            if(tab[(int)((e4.angle_fin-e4.angle_debut)/2.0+e4.angle_debut)] == -1){e4_vide = 1;e4.vide = 1;}
            if(tab[(int)((e5.angle_fin-e5.angle_debut)/2.0+e5.angle_debut)] == -1){e5_vide = 1;e5.vide = 1;}
            if(tab[(int)((e6.angle_fin-e6.angle_debut)/2.0+e6.angle_debut)] == -1){e6_vide = 1;e6.vide = 1;}

            e1_vide *= (e1.angle_fin-e1.angle_debut);
            e2_vide *= (e2.angle_fin-e2.angle_debut);
            e3_vide *= (e3.angle_fin-e3.angle_debut);
            e4_vide *= (e4.angle_fin-e4.angle_debut);
            e5_vide *= (e5.angle_fin-e5.angle_debut);
            e6_vide *= (e6.angle_fin-e6.angle_debut);

            break;
            }
         case 7:
            {
            if(tab[(int)((e1.angle_fin-e1.angle_debut)/2.0+e1.angle_debut)] == -1){e1_vide = 1;e1.vide = 1;}
            if(tab[(int)((e2.angle_fin-e2.angle_debut)/2.0+e2.angle_debut)] == -1){e2_vide = 1;e2.vide = 1;}
            if(tab[(int)((e3.angle_fin-e3.angle_debut)/2.0+e3.angle_debut)] == -1){e3_vide = 1;e3.vide = 1;}
            if(tab[(int)((e4.angle_fin-e4.angle_debut)/2.0+e4.angle_debut)] == -1){e4_vide = 1;e4.vide = 1;}
            if(tab[(int)((e5.angle_fin-e5.angle_debut)/2.0+e5.angle_debut)] == -1){e5_vide = 1;e5.vide = 1;}
            if(tab[(int)((e6.angle_fin-e6.angle_debut)/2.0+e6.angle_debut)] == -1){e6_vide = 1;e6.vide = 1;}
            if(tab[(int)((e7.angle_fin-e7.angle_debut)/2.0+e7.angle_debut)] == -1){e7_vide = 1;e7.vide = 1;}

            e1_vide *= (e1.angle_fin-e1.angle_debut);
            e2_vide *= (e2.angle_fin-e2.angle_debut);
            e3_vide *= (e3.angle_fin-e3.angle_debut);
            e4_vide *= (e4.angle_fin-e4.angle_debut);
            e5_vide *= (e5.angle_fin-e5.angle_debut);
            e6_vide *= (e6.angle_fin-e6.angle_debut);
            e7_vide *= (e7.angle_fin-e7.angle_debut);

            break;
            }
         case 8:
            {
            if(tab[(int)((e1.angle_fin-e1.angle_debut)/2.0+e1.angle_debut)] == -1){e1_vide = 1;e1.vide = 1;}
            if(tab[(int)((e2.angle_fin-e2.angle_debut)/2.0+e2.angle_debut)] == -1){e2_vide = 1;e2.vide = 1;}
            if(tab[(int)((e3.angle_fin-e3.angle_debut)/2.0+e3.angle_debut)] == -1){e3_vide = 1;e3.vide = 1;}
            if(tab[(int)((e4.angle_fin-e4.angle_debut)/2.0+e4.angle_debut)] == -1){e4_vide = 1;e4.vide = 1;}
            if(tab[(int)((e5.angle_fin-e5.angle_debut)/2.0+e5.angle_debut)] == -1){e5_vide = 1;e5.vide = 1;}
            if(tab[(int)((e6.angle_fin-e6.angle_debut)/2.0+e6.angle_debut)] == -1){e6_vide = 1;e6.vide = 1;}
            if(tab[(int)((e7.angle_fin-e7.angle_debut)/2.0+e7.angle_debut)] == -1){e7_vide = 1;e7.vide = 1;}
            if(tab[(int)((e8.angle_fin-e8.angle_debut)/2.0+e8.angle_debut)] == -1){e8_vide = 1;e8.vide = 1;}

            e1_vide *= (e1.angle_fin-e1.angle_debut);
            e2_vide *= (e2.angle_fin-e2.angle_debut);
            e3_vide *= (e3.angle_fin-e3.angle_debut);
            e4_vide *= (e4.angle_fin-e4.angle_debut);
            e5_vide *= (e5.angle_fin-e5.angle_debut);
            e6_vide *= (e6.angle_fin-e6.angle_debut);
            e7_vide *= (e7.angle_fin-e7.angle_debut);
            e8_vide *= (e8.angle_fin-e8.angle_debut);

            break;
            }
         case 9:
            {
            if(tab[(int)((e1.angle_fin-e1.angle_debut)/2.0+e1.angle_debut)] == -1){e1_vide = 1;e1.vide = 1;}
            if(tab[(int)((e2.angle_fin-e2.angle_debut)/2.0+e2.angle_debut)] == -1){e2_vide = 1;e2.vide = 1;}
            if(tab[(int)((e3.angle_fin-e3.angle_debut)/2.0+e3.angle_debut)] == -1){e3_vide = 1;e3.vide = 1;}
            if(tab[(int)((e4.angle_fin-e4.angle_debut)/2.0+e4.angle_debut)] == -1){e4_vide = 1;e4.vide = 1;}
            if(tab[(int)((e5.angle_fin-e5.angle_debut)/2.0+e5.angle_debut)] == -1){e5_vide = 1;e5.vide = 1;}
            if(tab[(int)((e6.angle_fin-e6.angle_debut)/2.0+e6.angle_debut)] == -1){e6_vide = 1;e6.vide = 1;}
            if(tab[(int)((e7.angle_fin-e7.angle_debut)/2.0+e7.angle_debut)] == -1){e7_vide = 1;e7.vide = 1;}
            if(tab[(int)((e8.angle_fin-e8.angle_debut)/2.0+e8.angle_debut)] == -1){e8_vide = 1;e8.vide = 1;}
            if(tab[(int)((e9.angle_fin-e9.angle_debut)/2.0+e9.angle_debut)] == -1){e9_vide = 1;e9.vide = 1;}

            e1_vide *= (e1.angle_fin-e1.angle_debut);
            e2_vide *= (e2.angle_fin-e2.angle_debut);
            e3_vide *= (e3.angle_fin-e3.angle_debut);
            e4_vide *= (e4.angle_fin-e4.angle_debut);
            e5_vide *= (e5.angle_fin-e5.angle_debut);
            e6_vide *= (e6.angle_fin-e6.angle_debut);
            e7_vide *= (e7.angle_fin-e7.angle_debut);
            e8_vide *= (e8.angle_fin-e8.angle_debut);
            e9_vide *= (e9.angle_fin-e9.angle_debut);

            break;
            }
         case 10:
            {
            if(tab[(int)((e1.angle_fin-e1.angle_debut)/2.0+e1.angle_debut)] == -1){e1_vide = 1;e1.vide = 1;}
            if(tab[(int)((e2.angle_fin-e2.angle_debut)/2.0+e2.angle_debut)] == -1){e2_vide = 1;e2.vide = 1;}
            if(tab[(int)((e3.angle_fin-e3.angle_debut)/2.0+e3.angle_debut)] == -1){e3_vide = 1;e3.vide = 1;}
            if(tab[(int)((e4.angle_fin-e4.angle_debut)/2.0+e4.angle_debut)] == -1){e4_vide = 1;e4.vide = 1;}
            if(tab[(int)((e5.angle_fin-e5.angle_debut)/2.0+e5.angle_debut)] == -1){e5_vide = 1;e5.vide = 1;}
            if(tab[(int)((e6.angle_fin-e6.angle_debut)/2.0+e6.angle_debut)] == -1){e6_vide = 1;e6.vide = 1;}
            if(tab[(int)((e7.angle_fin-e7.angle_debut)/2.0+e7.angle_debut)] == -1){e7_vide = 1;e7.vide = 1;}
            if(tab[(int)((e8.angle_fin-e8.angle_debut)/2.0+e8.angle_debut)] == -1){e8_vide = 1;e8.vide = 1;}
            if(tab[(int)((e9.angle_fin-e9.angle_debut)/2.0+e9.angle_debut)] == -1){e9_vide = 1;e9.vide = 1;}
            if(tab[(int)((e10.angle_fin-e10.angle_debut)/2.0+e10.angle_debut)] == -1){e10_vide = 1;e10.vide = 1;}

            e1_vide *= (e1.angle_fin-e1.angle_debut);
            e2_vide *= (e2.angle_fin-e2.angle_debut);
            e3_vide *= (e3.angle_fin-e3.angle_debut);
            e4_vide *= (e4.angle_fin-e4.angle_debut);
            e5_vide *= (e5.angle_fin-e5.angle_debut);
            e6_vide *= (e6.angle_fin-e6.angle_debut);
            e7_vide *= (e7.angle_fin-e7.angle_debut);
            e8_vide *= (e8.angle_fin-e8.angle_debut);
            e9_vide *= (e9.angle_fin-e9.angle_debut);
            e10_vide*= (e10.angle_fin-e10.angle_debut);
            break;
            }
        }

    for(i=0;i != 10;i++)
    {
        switch(a)
            {
                case 0:
                    {
                    if ((e1_vide > e2_vide )&&(e1_vide > e3_vide)&&(e1_vide > e4_vide)&&(e1_vide > e5_vide)&&(e1_vide > e6_vide )&&(e1_vide > e7_vide)&&(e1_vide > e8_vide)&&(e1_vide > e9_vide)&&(e1_vide > e10_vide))
                        {result = (e1.angle_fin - e1.angle_debut)/2.0+ e1.angle_debut;}
                    else {  a = 1; }
                    break;
                    }
                case 1:
                    {
                    if ((e2_vide > e1_vide )&&(e2_vide > e3_vide)&&(e2_vide > e4_vide)&&(e2_vide > e5_vide)&&(e2_vide > e6_vide )&&(e2_vide > e7_vide)&&(e2_vide > e8_vide)&&(e2_vide > e9_vide)&&(e2_vide > e10_vide))
                        { result = (e2.angle_fin - e2.angle_debut)/2.0+ e2.angle_debut;}
                    else  { a = 2;  }
                    break;
                    }
                case 2:
                    {
                    if ((e3_vide > e1_vide )&&(e3_vide > e2_vide)&&(e3_vide > e4_vide)&&(e3_vide > e5_vide)&&(e3_vide > e6_vide )&&(e3_vide > e7_vide)&&(e3_vide > e8_vide)&&(e3_vide > e9_vide)&&(e3_vide > e10_vide))
                        {result = (e3.angle_fin - e3.angle_debut)/2.0+ e3.angle_debut; }
                    else {  a = 3;}
                    break;
                    }
                case 3:
                    {
                    if ((e4_vide > e1_vide )&&(e4_vide > e2_vide)&&(e4_vide > e3_vide)&&(e4_vide > e5_vide)&&(e4_vide > e6_vide )&&(e4_vide > e7_vide)&&(e4_vide > e8_vide)&&(e4_vide > e9_vide)&&(e4_vide > e10_vide))
                        { result = (e4.angle_fin - e4.angle_debut)/2.0+ e4.angle_debut;}
                    else { a = 4; }
                    break;
                    }
                case 4:
                    {
                    if ((e5_vide > e1_vide )&&(e5_vide > e2_vide)&&(e5_vide > e3_vide)&&(e5_vide > e4_vide)&&(e5_vide > e6_vide )&&(e5_vide > e7_vide)&&(e5_vide > e8_vide)&&(e5_vide > e9_vide)&&(e5_vide > e10_vide))
                        {result = (e5.angle_fin - e5.angle_debut)/2.0+ e5.angle_debut;}
                    else { a = 5;  }
                    break;
                    }
                case 5:
                    {
                    if ((e6_vide > e1_vide )&&(e6_vide > e2_vide)&&(e6_vide > e3_vide)&&(e6_vide > e4_vide)&&(e6_vide > e5_vide )&&(e6_vide > e7_vide)&&(e6_vide > e8_vide)&&(e6_vide > e9_vide)&&(e6_vide > e10_vide))
                        {   result = (e6.angle_fin - e6.angle_debut)/2.0+ e6.angle_debut;}
                    else {a = 6;}
                    break;
                    }
                case 6:
                    {
                    if ((e7_vide > e1_vide )&&(e7_vide > e2_vide)&&(e7_vide > e3_vide)&&(e7_vide > e4_vide)&&(e7_vide > e5_vide )&&(e7_vide > e6_vide)&&(e7_vide > e8_vide)&&(e7_vide > e9_vide)&&(e7_vide > e10_vide))
                        {result = (e7.angle_fin - e7.angle_debut)/2.0+ e7.angle_debut;  }
                    else{ a = 7; }
                    break;
                    }
                case 7:
                    {
                    if ((e8_vide > e1_vide )&&(e8_vide > e2_vide)&&(e8_vide > e3_vide)&&(e8_vide > e4_vide)&&(e8_vide > e5_vide )&&(e8_vide > e6_vide)&&(e8_vide > e7_vide)&&(e8_vide > e9_vide)&&(e8_vide > e10_vide))
                        { result = (e8.angle_fin - e8.angle_debut)/2.0+ e8.angle_debut;}
                    else
                        { a = 8;}
                    break;
                    }
               case 8:
                    {
                    if ((e9_vide > e1_vide )&&(e9_vide > e2_vide)&&(e9_vide > e3_vide)&&(e9_vide > e4_vide)&&(e9_vide > e5_vide )&&(e9_vide > e6_vide)&&(e9_vide > e7_vide)&&(e9_vide > e8_vide)&&(e9_vide > e10_vide))
                        {result = (e9.angle_fin - e9.angle_debut)/2.0+ e9.angle_debut;}
                    else{a = 9;}
                    break;
                    }
                case 9:
                    {
                    if ((e10_vide > e1_vide )&&(e10_vide > e2_vide)&&(e10_vide > e3_vide)&&(e10_vide > e4_vide)&&(e10_vide > e5_vide )&&(e10_vide > e6_vide)&&(e10_vide > e7_vide)&&(e10_vide > e8_vide)&&(e10_vide > e9_vide))
                        { result = (e10.angle_fin - e10.angle_debut)/2.0+ e10.angle_debut;}
                    break;
                    }
            }
    }

    if (result < 90){result =  90 - result;result = -result ;}

    if (result == 90){result = 0; }

    if (result > 90){ result =   result - 90 ;}

return result;
}

#include <sys/stat.h>
#include <stdio.h>
#include <stdlib.h>
#include <math.h>
#define taille 181

struct Ensemble{
float debut;
float fin;
    int vide;

float angle_debut;
float angle_fin;

    float distance_debut;
float distance_fin;
float size;

};

const char* filename = "input.txt";
float lissage(float tab[taille]);
float choix_angle(int cs,float tab[taille],struct Ensemble e1, struct Ensemble e2, struct Ensemble e3, struct Ensemble e4, struct Ensemble e5, struct Ensemble e6 , struct Ensemble e7, struct Ensemble e8, struct Ensemble e9, struct Ensemble e10);

int main(int argc, char *argv[])
{
    struct Ensemble e1 = {0,0,0};
    struct Ensemble e2 = {0,0,0};
    struct Ensemble e3 = {0,0,0};
    struct Ensemble e4 = {0,0,0};
    struct Ensemble e5 = {0,0,0};
    struct Ensemble e6 = {0,0,0};
    struct Ensemble e7 = {0,0,0};
    struct Ensemble e8 = {0,0,0};
    struct Ensemble e9 = {0,0,0};
    struct Ensemble e10 = {0,0,0};

    int i,o;
    char cs=0;
    float valeur = 0, angle_roues, vitesse;   // Vmax-0.5*ln(|x|)-0.01*exp(|x|)

    float tab[taille];

    int u=0;

//--------------------------------------------------------------                recuperation donées fichier texte
    FILE *in_file = fopen(filename, "r");

    struct stat sb;
    stat(filename, &sb);

    char *file_contents = malloc(sb.st_size);

        while (fscanf(in_file, "%[^\n] ", file_contents) != EOF)
            {

            tab[u] =  atof(file_contents);
            u++;
            }

    fclose(in_file);
//--------------------------------------------------------------

for(o=0;o!=80;o++)//while(1)
    {
    lissage(tab);

    for(i=1; i!=taille+1; i++)
        {
            valeur =((tab[i])/(tab[i+1]));

            e1.debut = 0;
            e1.angle_debut = 1;
            e1.distance_debut = tab[1];

            switch(cs){

            case 0:{
                if (!((valeur<1.05)&&(valeur>0.95))){

                    e1.fin = i;
                    e1.angle_fin = i;
                    e1.distance_fin = tab[i];

                    e2.debut = i+1;
                    e2.angle_debut = i+1;
                    e2.distance_debut = tab[i+1];

                    cs = 1;}
                break;}

            case 1:{
                if (!((valeur<1.05)&&(valeur>0.95))){

                    e2.fin = i;
                    e2.angle_fin = i;
                    e2.distance_fin = tab[i];
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

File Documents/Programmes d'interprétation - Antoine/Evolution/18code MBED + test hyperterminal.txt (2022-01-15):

#include "mbed.h"
#include <cstdio>
#include <string>
#include <stdio.h>
#include <stdlib.h>
#include <math.h>

#define taille 181

//#include "bluetooth.h"
#include "car.h"

Serial PC(USBTX,USBRX, 9600);
#include "lidar.h"

struct Ensemble {
    float debut;
    float fin;
    float vide;

    float angle_debut;
    float angle_fin;

    float distance_debut;
    float distance_fin;
    float size;

};
struct datapoint {

    float angle;
    float distance;
    int ensemble;
};

float lissage(float tab[taille]);
float choix_angle(int cs,float tab[taille],struct Ensemble e1, struct Ensemble e2, struct Ensemble e3, struct Ensemble e4, struct Ensemble e5, struct Ensemble e6, struct Ensemble e7, struct Ensemble e8, struct Ensemble e9, struct Ensemble e10);

int main()
{
    initWheels();

    struct Ensemble e1 = {0,0,0};
    struct Ensemble e2 = {0,0,0};
    struct Ensemble e3 = {0,0,0};
    struct Ensemble e4 = {0,0,0};
    struct Ensemble e5 = {0,0,0};
    struct Ensemble e6 = {0,0,0};
    struct Ensemble e7 = {0,0,0};
    struct Ensemble e8 = {0,0,0};
    struct Ensemble e9 = {0,0,0};
    struct Ensemble e10 = {0,0,0};

    int i,o;
    char cs=0;
    float valeur = 0, angle_roues = 0, angle_roues_final, vitesse;
    float mem[3];

    int u=0;

    float tab[181];
datapoint tab_data[181];
    initLidar();
    //  initBLE();
    mem[0]=0;
    mem[1]=0;
    mem[2]=0;
    while (1) {
        getLidarData(tab);
        //  sendOverBluetooth(data);
for(i=1; i!=8; i++) {
        lissage(tab);
        }

datapoint CePoint;

 for(i=0; i!=taille+1; i++) {
         tab_data[i].distance = tab[i];
         tab_data[i].angle = i;
         tab_data[i].ensemble = 0;
        }//fin for(i=1; i!=taille+1; i++)
        cs = 0;
       
        for(i=1; i!=taille+1; i++) {
            valeur =((tab[i])+(tab[i+1])+0.00001)/((tab[i])*2.0+0.00001);

            if((valeur>0.8)&&(valeur<1.2)) {
                //PC.printf("tab[%d] = %lf   valeur = %lf\n\r",i,tab[i],valeur);
            } else {
                PC.printf("tab[%d] = %lf   valeur = %lf\t\tsaut ----------\n\r",i,tab[i],valeur);
            }
            e1.debut = 0;
            e1.angle_debut = 1;
            e1.distance_debut = tab[1];

valeur = ( tab_data[i].distance+0.00001 / tab_data[i-1].distance+0.00001);
           switch(cs) {

                case 0: {
                    if (!((valeur<1.5)&&(valeur>0.50))) {

                        e1.fin = i;
                        e1.angle_fin = i;
                        e1.distance_fin = tab[i];

                        e2.debut = i+1;
                        e2.angle_debut = i+1;
                        e2.distance_debut = tab[i+1];

                        cs = 1;
                    }
                    else        
                    {
                        tab_data[i].ensemble = 1;
                        e1.size += 1;
                    }
                    break;
                }

                case 1: {
                    if (!((valeur<1.5)&&(valeur>0.50)))  {

                        e2.fin = i;
                        e2.angle_fin = i;
                        e2.distance_fin = tab[i];

                        e3.debut = i+1;
                        e3.angle_debut = i+1;
                        e3.distance_debut = tab[i+1];

                        cs = 2;
                    }
                         else        
                    {
                        tab_data[i].ensemble = 2;
                        e2.size += 1;
                    }
                    break;
                }

                case 2: {
                    if (!((valeur<1.5)&&(valeur>0.50)))  {

                        e3.fin = i;
                        e3.angle_fin = i;
                        e3.distance_fin = tab[i];
                        if(i<179) {
                            e4.debut = i+1;
                            e4.angle_debut = i+1;
                            e4.distance_debut = tab[i+1];

                            cs = 3;
                        }
                    }
                         else        
                    {
                        tab_data[i].ensemble = 3;
                        e3.size += 1;
                    }
                    break;
                }

                case 3: {
                    if (!((valeur<1.5)&&(valeur>0.50)))  {

                        e4.fin = i;
                        e4.angle_fin = i;
                        e4.distance_fin = tab[i];
                        if(i<179) {
                            e5.debut = i+1;
                            e5.angle_debut = i+1;
                            e5.distance_debut = tab[i+1];

                            cs = 4;
                        }
                    }
                         else        
                    {
                        tab_data[i].ensemble = 4;
                        e4.size += 1;
                    }
                   
                    break;
                }

                case 4: {
                    if (!((valeur<1.5)&&(valeur>0.50)))  {

                        e5.fin = i;
                        e5.angle_fin = i;
                        e5.distance_fin = tab[i];
                        if(i<179) {
                            e6.debut = i+1;
                            e6.angle_debut = i+1;
                            e6.distance_debut = tab[i+1];

                            cs = 5;
                        }
                    }
                         else        
                    {
                        tab_data[i].ensemble = 5;
                        e5.size += 1;
                    }
                    break;
                }

                case 5: {
                    if (!((valeur<1.5)&&(valeur>0.50)))  {

                        e6.fin = i;
                        e6.angle_fin = i;
                        e6.distance_fin = tab[i];
                        if(i<179) {
                            e7.debut = i+1;
                            e7.angle_debut = i+1;
                            e7.distance_debut = tab[i+1];

                            cs = 6;
                        }
                    }
                         else        
                    {
                        tab_data[i].ensemble = 6;
                        e6.size += 1;
                    }
                    break;
                }

                case 6: {
                    if (!((valeur<1.5)&&(valeur>0.50)))  {

                        e7.fin = i;
                        e7.angle_fin = i;
                        e7.distance_fin = tab[i];
                        if(i<179) {
                            e8.debut = i+1;
                            e8.angle_debut = i+1;
                            e8.distance_debut = tab[i+1];

                            cs = 7;
                        }
                    }
                         else        
                    {
                        tab_data[i].ensemble = 7;
                        e7.size += 1;
                    }
                    break;
                }

                case 7: {
                    if (!((valeur<1.5)&&(valeur>0.50)))  {

                        e8.fin = i;
                        e8.angle_fin = i;
                        e8.distance_fin = tab[i];
                        if(i<179) {
                            e9.debut = i+1;
                            e9.angle_debut = i+1;
                            e9.distance_debut = tab[i+1];

                            cs = 8;
                        }
                    }
                         else        
                    {
                        tab_data[i].ensemble = 8;
                        e8.size += 1;
                    }
                    break;
                }

                case 8: {
                    if(!((valeur<1.5)&&(valeur>0.50)))  {

                        e9.fin = i;
                        e9.angle_fin = i;
                        e9.distance_fin = tab[i];

                        if(i<179) {
                            e10.debut = i+1;
                            e10.angle_debut = i+1;
                            e10.distance_debut = tab[i+1];

                            cs = 9;
                        }
                    }
                         else        
                    {
                        tab_data[i].ensemble = 9;
                        e9.size += 1;
                    }
                    break;
                }

                case 9: {
                    if (!((valeur<1.5)&&(valeur>0.50)))  {

                        e10.fin = i;
                        e10.angle_fin = i;
                        e10.distance_fin = tab[i];

                    }
                         else        
                    {
                        tab_data[i].ensemble = 10;
                        e10.size += 1;
                    }
                        break;
                   
                }
            }

        }//fin for(i=1; i!=taille+1; i++)

        angle_roues = choix_angle(cs,tab,e1, e2, e3, e4, e5,e6,e7,e8,e9,e10);
        PC.printf("\n\r\n\r         angle_roues =     %lf\n\r\n\r\n\r",choix_angle(cs,tab,e1, e2, e3, e4, e5,e6,e7,e8,e9,e10));

        mem[2]=mem[1];
        mem[1]=mem[0];
        mem[0]=angle_roues ;

        angle_roues_final = ( mem[2] + mem[1] + mem[0] ) /3.0;

        turn(angle_roues_final);
        cs = 0;

    }//fin while

    return 0;

} //fin main ''''''''''''''''''''''''''''''''''''''''''''''''''''''''''''

float lissage(float tab[taille])
{

    int i=0;
    float valeur2;

    if(tab[0]>150)tab[0]=-1;

    for(i=1; i<=taille; i++) { //lissage
        //tab[i]=tab[i] * (asin ( (double)i ));  //projection

        if(tab[i]>150)tab[i]=-1; //bride

        valeur2 = ((tab[i-1]+0.00001)/(tab[i+1]+0.00001));
        if ((((tab[i]+0.00001)/(tab[i+1]+0.00001))>1.05) || (((tab[i]+0.00001)/(tab[i+1]+0.00001))<0.95)) {
            if (((valeur2<1.5)&(valeur2>0.5))) {
                tab[i] = tab[i-1];
                //   PC.printf("%lf\n\r",tab[i]);
               
                 //PC.printf("tab[%d] = %lf\t  tab[%d]= %lf\t tab[%d] = %lf\n\r",i-1,tab[i-1],i+1,tab[i+1],i,tab[i]);
            }
        }
    }
}

float choix_angle(int cs,float tab[taille],struct Ensemble e1, struct Ensemble e2, struct Ensemble e3, struct Ensemble e4, struct Ensemble e5, struct Ensemble e6, struct Ensemble e7, struct Ensemble e8, struct Ensemble e9, struct Ensemble e10)
{
    int e1_vide = 0,e2_vide = 0,e3_vide = 0,e4_vide = 0,e5_vide = 0,e6_vide = 0,e7_vide = 0,e8_vide = 0,e9_vide = 0,e10_vide = 0;
    int a=0,i;
    float result;
    cs +=1;

    if(tab[(int)(((int)e1.angle_fin-(int)e1.angle_debut)/2.0+(int)e1.angle_debut)] == -1) {
        e1_vide = 1;
    }
    if(tab[(int)(((int)e2.angle_fin-(int)e2.angle_debut)/2.0+(int)e2.angle_debut)] == -1) {
        e2_vide = 1;
    }
    if(tab[(int)(((int)e3.angle_fin-(int)e3.angle_debut)/2.0+(int)e3.angle_debut)] == -1) {
        e3_vide = 1;
    }
    if(tab[(int)(((int)e4.angle_fin-(int)e4.angle_debut)/2.0+(int)e4.angle_debut)] == -1) {
        e4.vide = 1;
    }
    if(tab[(int)(((int)e5.angle_fin-(int)e5.angle_debut)/2.0+(int)e5.angle_debut)] == -1) {
        e5_vide = 1;
    }
    if(tab[(int)(((int)e6.angle_fin-(int)e6.angle_debut)/2.0+(int)e6.angle_debut)] == -1) {
        e6.vide = 1;
    }
    if(tab[(int)(((int)e7.angle_fin-(int)e7.angle_debut)/2.0+(int)e7.angle_debut)] == -1) {
        e7.vide = 1;
    }
    if(tab[(int)(((int)e8.angle_fin-(int)e8.angle_debut)/2.0+(int)e8.angle_debut)] == -1) {
        e8_vide = 1;
    }
    if(tab[(int)(((int)e9.angle_fin-(int)e9.angle_debut)/2.0+(int)e9.angle_debut)] == -1) {
        e9_vide = 1;
    }
    if(tab[(int)(((int)e10.angle_fin-(int)e10.angle_debut)/2.0+(int)e10.angle_debut)] == -1) {
        e10_vide = 1;
    }
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

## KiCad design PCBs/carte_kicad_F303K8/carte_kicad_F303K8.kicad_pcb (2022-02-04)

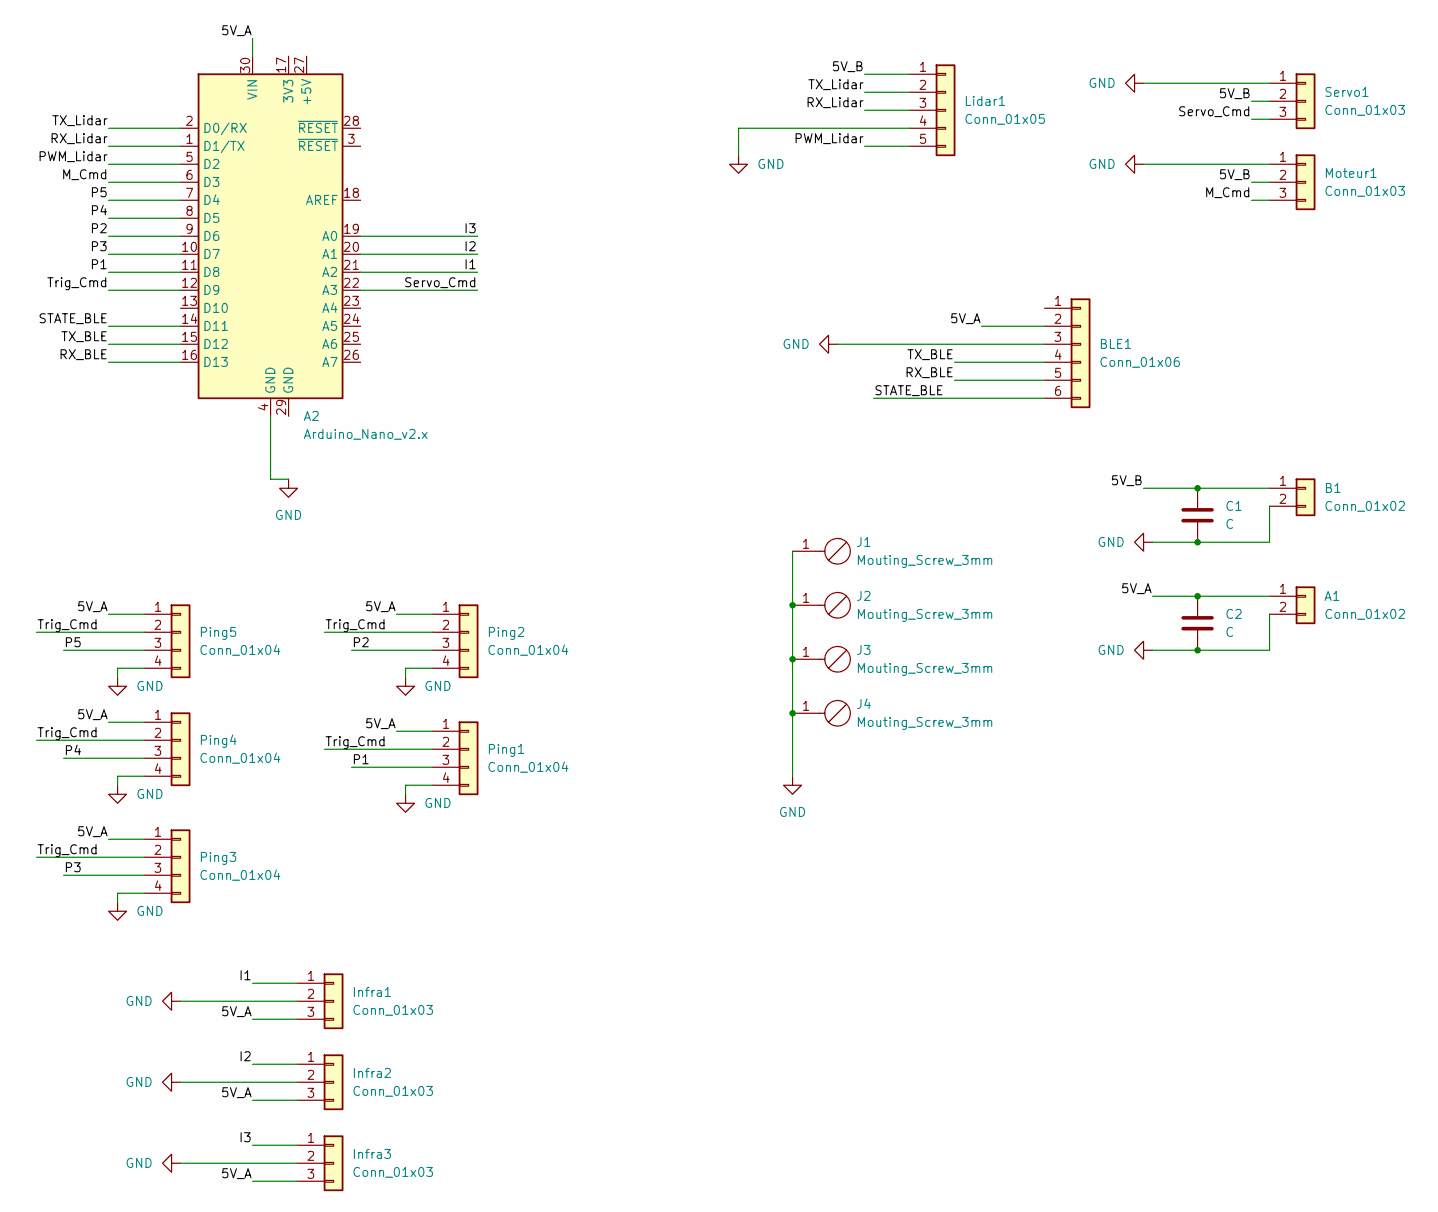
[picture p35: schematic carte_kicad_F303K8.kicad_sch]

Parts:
A1: Conn_01x02; PinHeader_1x02_P2.54mm_Vertical
A2: Arduino_Nano_v2.x; Arduino_Nano
B1: Conn_01x02; PinHeader_1x02_P2.54mm_Vertical
BLE1: Conn_01x06; PinHeader_1x06_P2.54mm_Vertical
C1, C2: C; C_Rect_L7.0mm_W2.5mm_P5.00mm
Infra1, Infra2, Infra3: Conn_01x03; PinHeader_1x03_P2.54mm_Vertical
J1, J2, J3, J4: Mouting_Screw_3mm
Lidar1: Conn_01x05; PinHeader_1x05_P2.54mm_Vertical
Moteur1: Conn_01x03; PinHeader_1x03_P2.54mm_Vertical
Ping1, Ping2, Ping3, Ping4, Ping5: Conn_01x04; PinHeader_1x04_P2.54mm_Vertical
Servo1: Conn_01x03; PinHeader_1x03_P2.54mm_Vertical

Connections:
/5V_A: A1.1, A2.30 (VIN), BLE1.2, C2.1, Infra1.3, Infra2.3, Infra3.3, Ping1.1, Ping2.1, Ping3.1, Ping4.1, Ping5.1
/5V_B: B1.1, C1.1, Lidar1.1, Moteur1.2, Servo1.2
/I1: A2.21 (A2), Infra1.1
/I2: A2.20 (A1), Infra2.1
/I3: A2.19 (A0), Infra3.1
/M_Cmd: A2.6 (D3), Moteur1.3
/P1: A2.11 (D8), Ping1.3
/P2: A2.9 (D6), Ping2.3
/P3: A2.10 (D7), Ping3.3
/P4: A2.8 (D5), Ping4.3
/P5: A2.7 (D4), Ping5.3
/PWM_Lidar: A2.5 (D2), Lidar1.5
/RX_BLE: A2.16 (D13), BLE1.5
/RX_Lidar: A2.1 (D1/TX), Lidar1.3
/STATE_BLE: A2.14 (D11), BLE1.6
/Servo_Cmd: A2.22 (A3), Servo1.3
/TX_BLE: A2.15 (D12), BLE1.4
/TX_Lidar: A2.2 (D0/RX), Lidar1.2
/Trig_Cmd: A2.12 (D9), Ping1.2, Ping2.2, Ping3.2, Ping4.2, Ping5.2
GND: A1.2, A2.4 (GND), B1.2, BLE1.3, C1.2, C2.2, Infra1.2, Infra2.2, Infra3.2, J1.1, J2.1, J3.1, J4.1, Lidar1.4, Moteur1.1, Ping1.4, Ping2.4, Ping3.4, Ping4.4, Ping5.4, Servo1.1

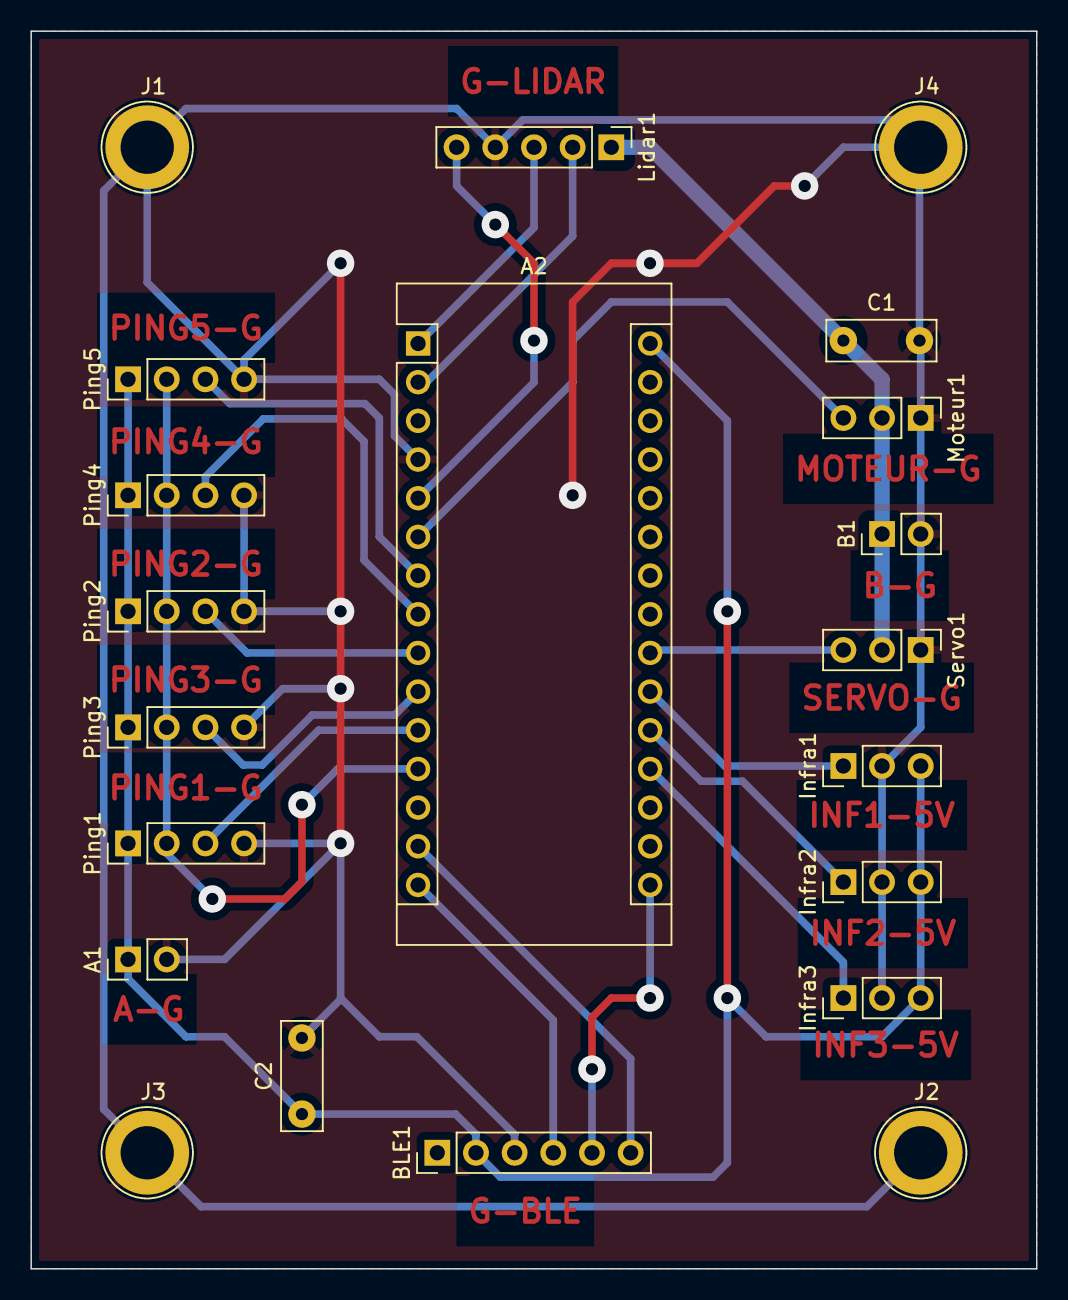
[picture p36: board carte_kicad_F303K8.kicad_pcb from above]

Board: 2 copper layers, 66.0 x 81.3 mm, 21 parts (0 on the bottom side), 20 nets.

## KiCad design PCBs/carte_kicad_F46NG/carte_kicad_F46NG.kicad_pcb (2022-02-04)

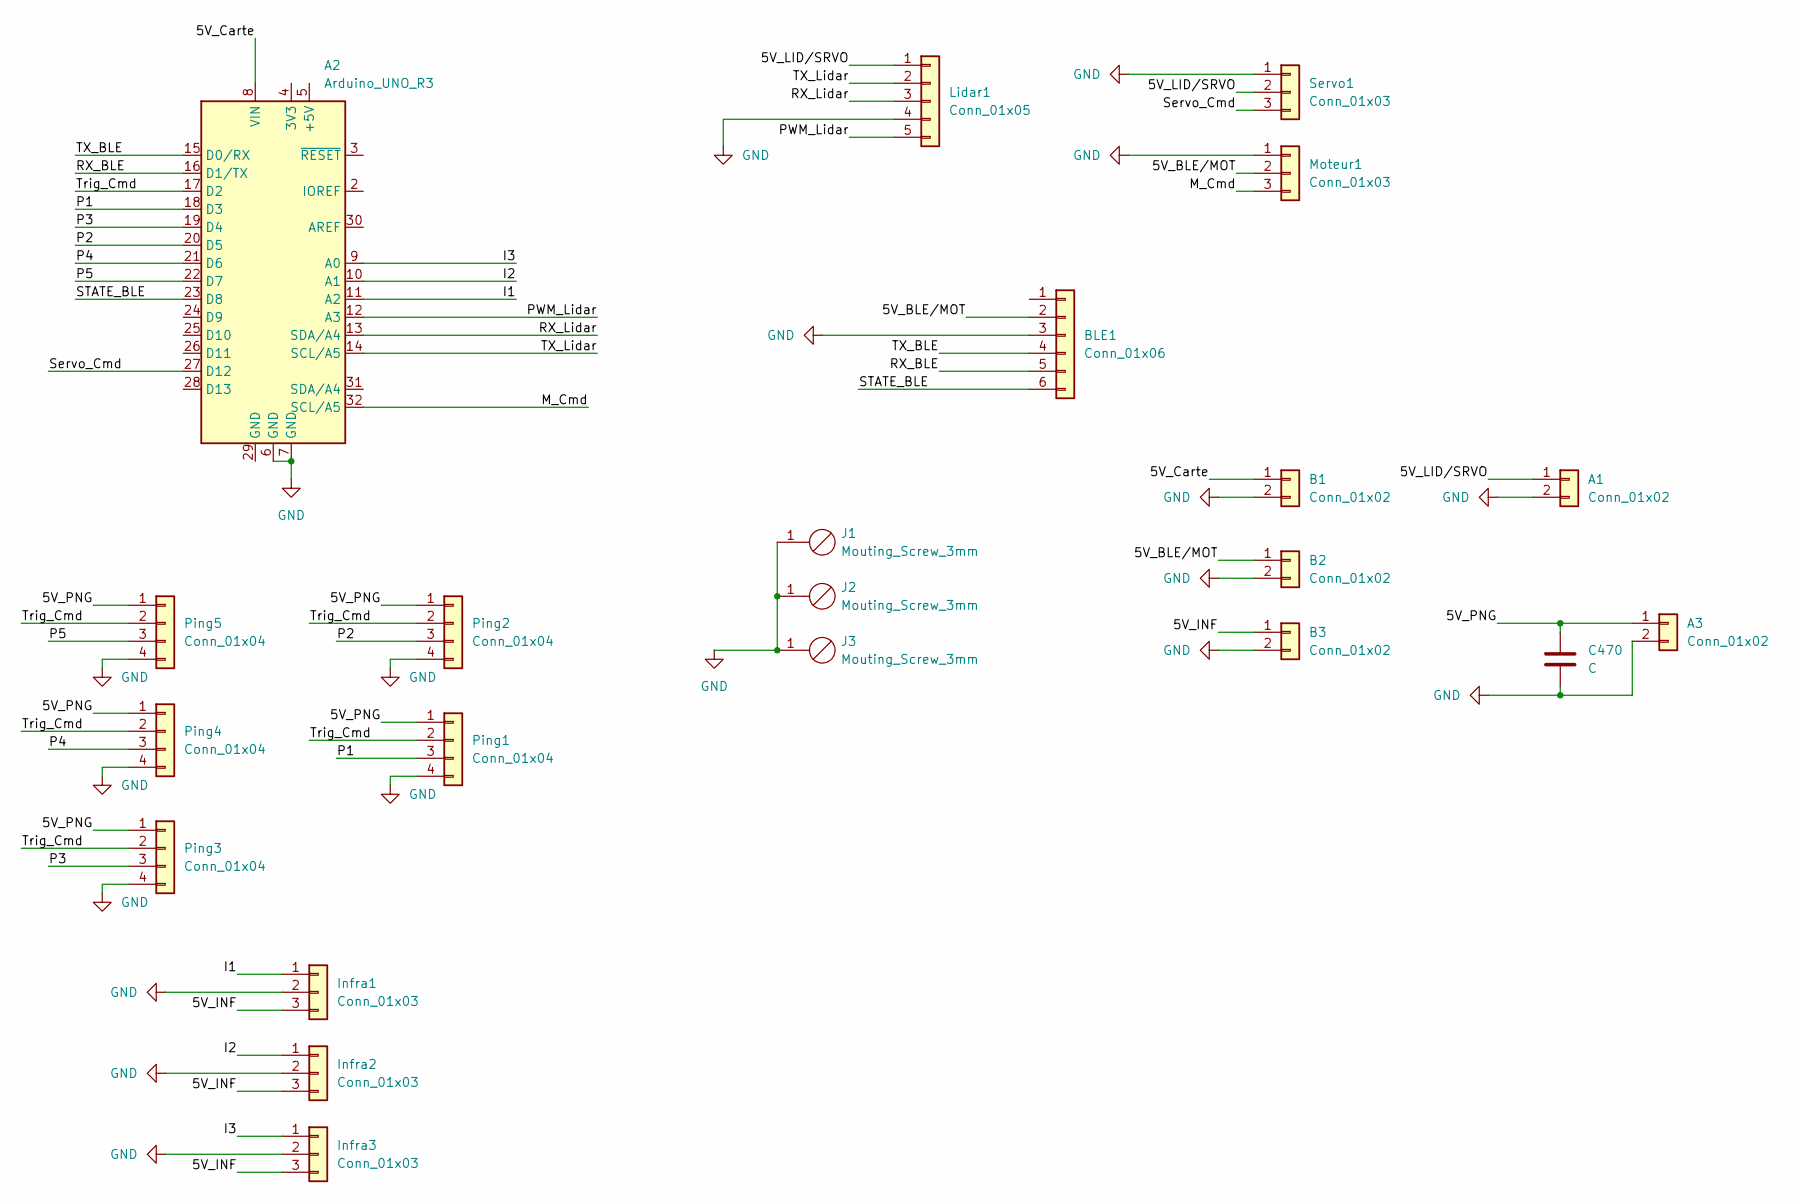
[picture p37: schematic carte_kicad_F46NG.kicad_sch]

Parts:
A1, A3: Conn_01x02; PinHeader_1x02_P2.54mm_Vertical
A2: Arduino_UNO_R3
B1, B2, B3: Conn_01x02; PinHeader_1x02_P2.54mm_Vertical
BLE1: Conn_01x06; PinHeader_1x06_P2.54mm_Vertical
C470: C; C_Rect_L7.0mm_W2.5mm_P5.00mm
Infra1, Infra2, Infra3: Conn_01x03; PinHeader_1x03_P2.54mm_Vertical
J1, J2, J3: Mouting_Screw_3mm
Lidar1: Conn_01x05; PinHeader_1x05_P2.54mm_Vertical
Moteur1: Conn_01x03; PinHeader_1x03_P2.54mm_Vertical
Ping1, Ping2, Ping3, Ping4, Ping5: Conn_01x04; PinHeader_1x04_P2.54mm_Vertical
Servo1: Conn_01x03; PinHeader_1x03_P2.54mm_Vertical

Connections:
/5V_BLE/MOT: B2.1, BLE1.2, Moteur1.2
/5V_Carte: A2.8 (VIN), B1.1
/5V_INF: B3.1, Infra1.3, Infra2.3, Infra3.3; also elsewhere on the board
/5V_LID/SRVO: A1.1, Lidar1.1, Servo1.2
/5V_PNG: A3.1, C470.1, Ping1.1, Ping2.1, Ping3.1, Ping4.1, Ping5.1
/I1: A2.11 (A2), Infra1.1
/I2: A2.10 (A1), Infra2.1
/I3: A2.9 (A0), Infra3.1; also elsewhere on the board
/M_Cmd: A2.32 (SCL/A5), Moteur1.3
/P1: A2.18 (D3), Ping1.3
/P2: A2.20 (D5), Ping2.3
/P3: A2.19 (D4), Ping3.3
/P4: A2.21 (D6), Ping4.3
/P5: A2.22 (D7), Ping5.3
/PWM_Lidar: A2.12 (A3), Lidar1.5
/RX_BLE: A2.16 (D1/TX), BLE1.5
/RX_Lidar: A2.13 (SDA/A4), Lidar1.3
/STATE_BLE: A2.23 (D8), BLE1.6
/Servo_Cmd: A2.27 (D12), Servo1.3
/TX_BLE: A2.15 (D0/RX), BLE1.4
/TX_Lidar: A2.14 (SCL/A5), Lidar1.2
/Trig_Cmd: A2.17 (D2), Ping1.2, Ping2.2, Ping3.2, Ping4.2, Ping5.2
GND: A1.2, A2.6 (GND), A2.7 (GND), A3.2, B1.2, B2.2, B3.2, BLE1.3, C470.2, Infra1.2, Infra2.2, Infra3.2, J1.1, J2.1, J3.1, Lidar1.4, Moteur1.1, Ping1.4, Ping2.4, Ping3.4, Ping4.4, Ping5.4, Servo1.1; also elsewhere on the board

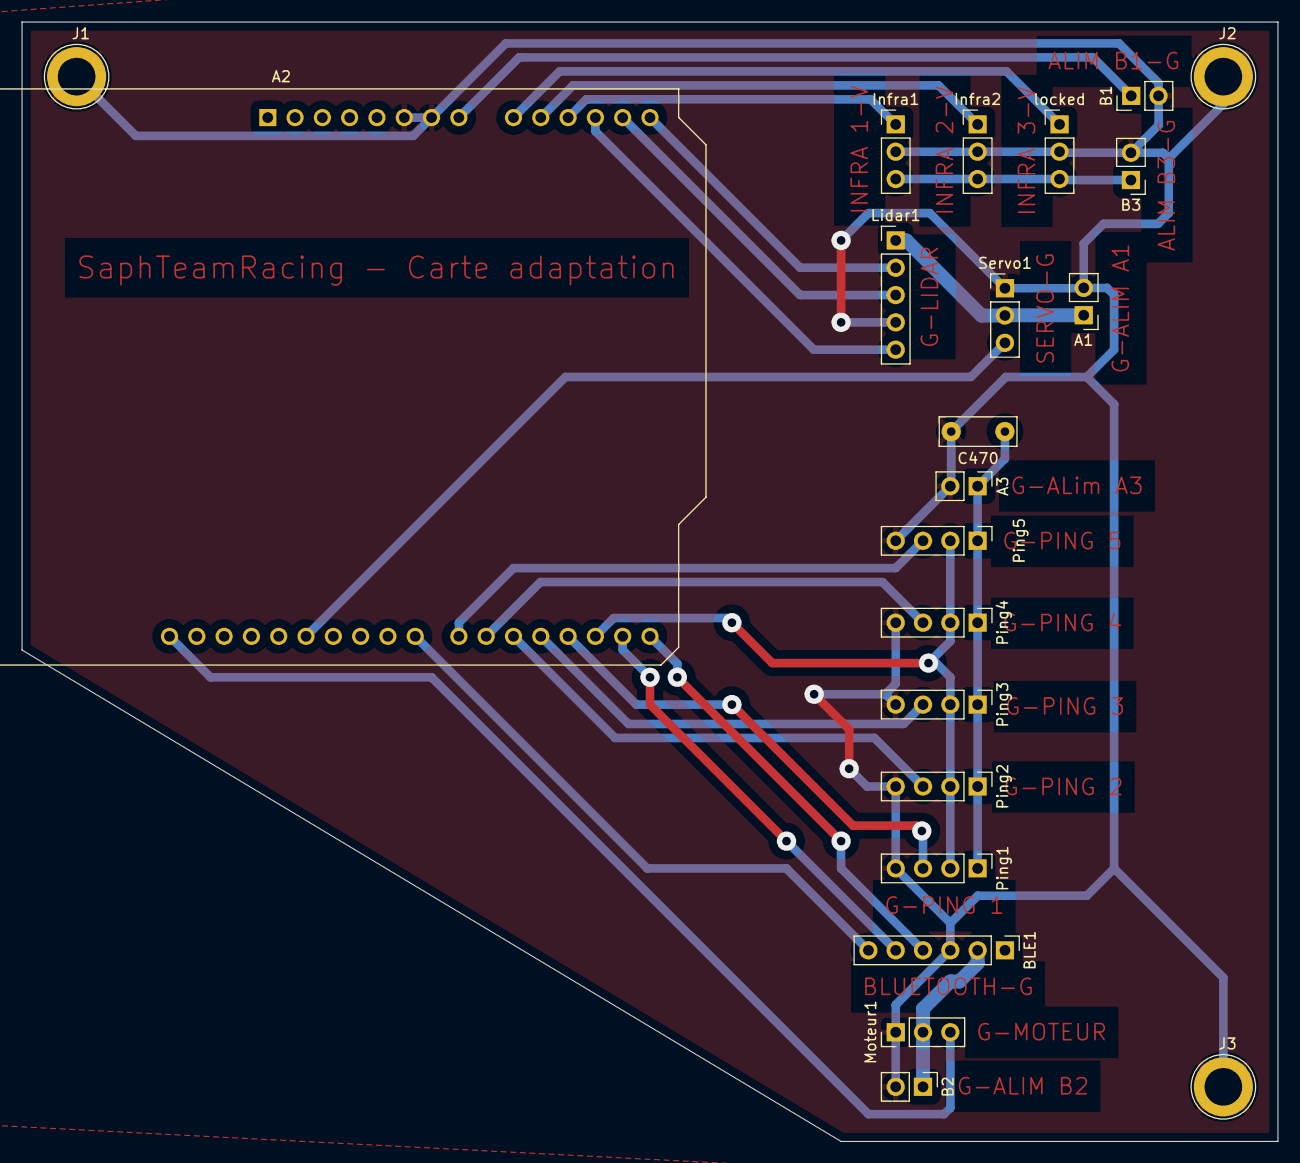
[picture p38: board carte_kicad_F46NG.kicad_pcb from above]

Board: 2 copper layers, 116.8 x 104.1 mm, 22 parts (0 on the bottom side), 23 nets.

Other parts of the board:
locked: Conn_01x03; PinHeader_1x03_P2.54mm_Vertical

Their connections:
/5V_INF: locked.3; also elsewhere on the board
/I3: locked.1; also elsewhere on the board
GND: locked.2; also elsewhere on the board

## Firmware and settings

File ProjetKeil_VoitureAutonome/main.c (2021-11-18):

#include <LPC17xx.h>
#include "GPIO.h"
#include "LPC_PWM.h"
#include "circular_buffer.h"


void write(char data);
void read(void);
void Init_BT (void);
void Init_Lidar (void);


int main(void) {
	initPWM();
	initPWMMoteur();
	initPWMServo();
	setPWMServo(50);
	setPWMServo(60);
	Init_BT;
	Init_Lidar;
	return 0;
}





void Init_BT (void) // broches P0.2 pour TX et P0.3 pour RX
{
	LPC_SC->PCONP |= (1<<3)//Active la sortie UART0 (active de base sur un reset)
	LPC_PINCON->PINSEL0 |= 0x5 << 4 ; // broches P0.2 pour TX et P0.3 pour RX
	LPC_UART0->FCR |= 1|(0x02<<6) //Active le FIFO et lance une interruption à la réception de 8 caractères
	LPC_UART0->LCR = 0x03 ; // 8 bits sans parité, 1 bit de stop
	// Réglage de la vitesse de transmission à 115200
	LPC_UART0->LCR |= 0x80 ; // Forçage bit DLAB=1 (Demande autorisation de modification)
	LPC_UART0->DLM = 0 ; // Pas de sur-division de PCLK
	LPC_UART0->DLL = 9 ; // Division principale par 9 de PLCK
	LPC_UART0->FDR = 0x21 ; // Division fractionnaire de 1,5 (DIVAddVAL=1 et MULVAL=2)
	LPC_UART0->LCR &= 0x7F ; // Forçage bit DLAB=0 (Fin d'autorisation de modification)
}

void Init_Lidar (void) // broches P0.2 pour TX et P0.3 pour RX
{
	LPC_SC->PCONP |= (1<<24)//Active la sortie UART2 (non active de base sur un reset)
	LPC_PINCON->PINSEL0 |= 0x5 << 20 ; // broches P0.10 pour TX et P0.11 pour RX
	LPC_UART2->FCR |= 1|(0x02<<6) //Active le FIFO et lance une interruption à la réception de 8 caractères
	LPC_UART0->LCR = 0x03 ; // 8 bits sans parité, 1 bit de stop
	// Réglage de la vitesse de transmission à 115200
	LPC_UART2->LCR |= 0x80 ; // Forçage bit DLAB=1 (Demande autorisation de modification)
	LPC_UART2->DLM = 0 ; // Pas de sur-division de PCLK
	LPC_UART2->DLL = 9 ; // Division principale par 9 de PLCK
	LPC_UART2->FDR = 0x21 ; // Division fractionnaire de 1,5 (DIVAddVAL=1 et MULVAL=2)
	LPC_UART2->LCR &= 0x7F ; // Forçage bit DLAB=0 (Fin d'autorisation de modification)
}

void read{
	static unsigned int i;
	while(!(UART0->LSR & (1<<0)){
		rawData[i] = UART0->RBR;
		i++;
	}
}

void write(data){
	while(!(UART0->LSR & (1<<5)){}
	UART0->THR = data;
}

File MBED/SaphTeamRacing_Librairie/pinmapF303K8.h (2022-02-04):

#ifndef _pinmapF303K8_h_
#define _pinmapF303K8_h_

// Lidar
#define TXLidar D1
#define RXLidar D0
#define PIN_PWM_Lidar D2

// Bluetooth
#define TXBle D12
#define RXBle D13
#define PIN_Status_Ble D1

// Ping
#define PIN_TriggerP D9
#define PING_IN_1 D8
#define PING_IN_2 D7
#define PING_IN_3 D6
#define PING_IN_4 D5
#define PING_IN_5 D4

// Infrared
#define INFRA_IN_1 A2
#define INFRA_IN_2 A1
#define INFRA_IN_3 A0

// Motor and servo
#define PINServo A3
#define PINMotor D3

#endif

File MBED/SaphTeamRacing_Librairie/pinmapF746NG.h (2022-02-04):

#ifndef _pinmapF746NG_h_
#define _pinmapF746NG_h_

// Lidar
#define TXLidar PF_6
#define RXLidar PF_7
#define PIN_PWM_Lidar PF_8

// Bluetooth
#define TXBle PC_7
#define RXBle PC_6
#define PIN_Status_Ble PI_2

// Ping
#define PIN_TriggerP PG_6
#define PING_IN_1 PB_4
#define PING_IN_2 PI_0
#define PING_IN_3 PG_7
#define PING_IN_4 PH_6
#define PING_IN_5 PI_3

// Infrared
#define INFRA_IN_1 PF_9
#define INFRA_IN_2 PF_10
#define INFRA_IN_3 PA_0

// Motor and servo
#define PINServo PB_14
#define PINMotor PB_8

#endif

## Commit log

2021-11-18 Ajoute les premiers fichiers de la carte KEIL
2021-12-05 ajoute la librairie Lidar
2021-12-05 Ajoute les instructions de la librairie
2021-12-05 Ajoute l'application de visualisation du LiDAR
2021-12-05 Perfectionne l'application de visualisation du LiDAR
2021-12-05 MAJ des instructions + complétion
2021-12-05 Actualise les librairies et introduit Car.h/Car.cpp
2021-12-09 Refonte bibliothèques, séparation de Lidar et BLE
2021-12-09 Update des directives
    Directives MAJ après l'ajout de bluetooth.h et bluetooth.c
2021-12-09 Séparation des scripts (refonte)
2021-12-28 Optimisation de la libaririe et corrections mineures
    [lidar.cpp, lidar.h]
2021-12-31 Améliore les performances
2022-01-02 Améliore les performances et résout des incohérences
2022-01-07 Corrige des erreurs
2022-01-15 Mise en forme pour le rapport de fin de semestre 3
    [AxelTraitement.PrjPcb, Carte_Keil_Emile_can_v0.SchDoc, Carte_Keil_Emile_proc_v0.SchDoc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]
2022-01-24 Modifie dossier lidar
2022-01-26 Met à jour des datasheets
2022-01-26 Ajoute le PCB kicad DISCO F746 NG
    [carte_kicad_F46NG.kicad_pcb, carte_kicad_F46NG.kicad_sch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]
2022-01-26 Met à jour le PCB kicad DISCO F746 NG
    [carte_kicad_F46NG.kicad_pcb, carte_kicad_F46NG.kicad_sch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]
2022-01-26 Met à jout les fichiers
    [plaque_chassis.dxf, plaque_lidar.dxf]
2022-01-27 MAJ le PCB
    [carte_kicad_F46NG.kicad_pcb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]
2022-01-27 Ajout des modèles 3D
    [Armature_lidar.stl, SRF04.stl]
2022-01-27 Ajoute une PINMAP en accord avec le PCB et met a jour les libairies
2022-02-04 Ajout du PCB pour F303K8
    [carte_kicad_F303K8.kicad_pcb, carte_kicad_F303K8.kicad_sch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]
2022-02-04 Ajoute la PINMAPF303K8
2022-02-07 MAJ rapport
    [SRF04.stl]
2022-02-07 Modifie la documentation
2022-02-07 Modifie les images
2022-02-24 Correction des bugs majeurs, version stable
    [car.cpp, car.h, lidar.cpp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]
